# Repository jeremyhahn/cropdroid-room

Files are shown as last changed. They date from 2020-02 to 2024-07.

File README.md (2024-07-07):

# cropdroid-room

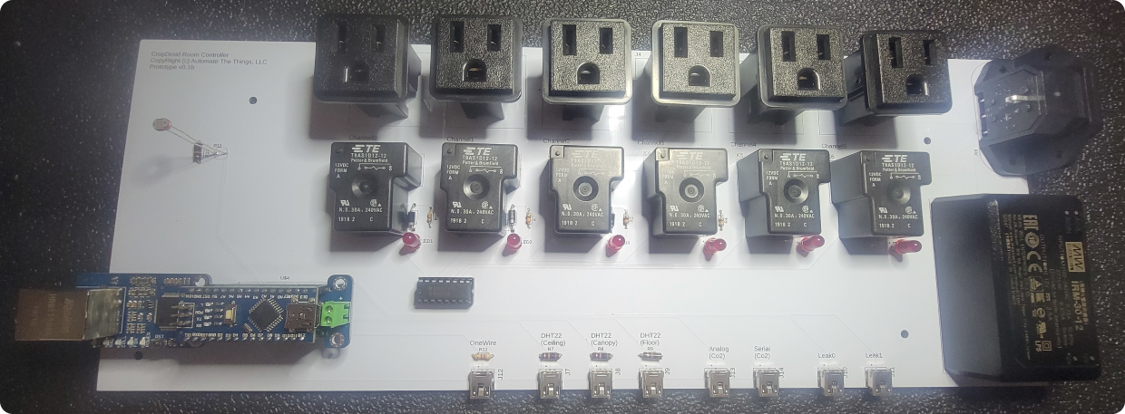
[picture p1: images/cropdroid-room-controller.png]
[](https://github.com/jeremyhahn/cropdroid-room)

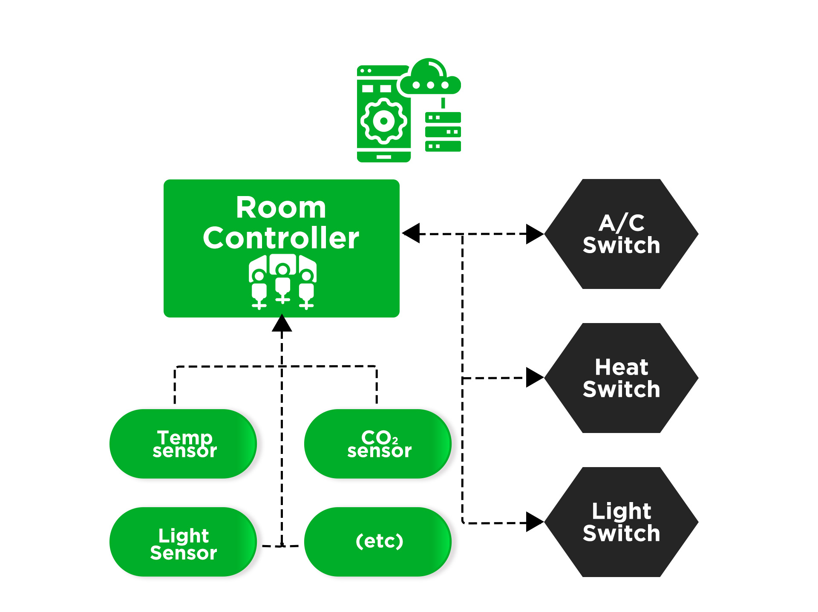
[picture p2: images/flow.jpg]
[](https://github.com/jeremyhahn/cropdroid-room)

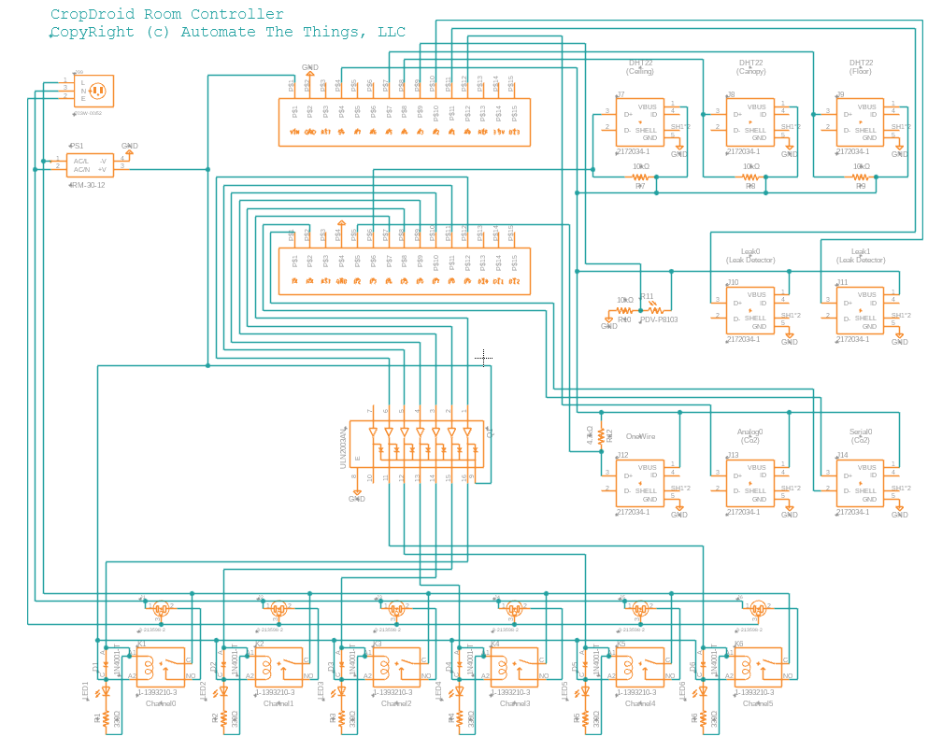
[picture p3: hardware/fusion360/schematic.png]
[](https://github.com/jeremyhahn/cropdroid-room/blob/master/hardware/fusion360/schematic.png)

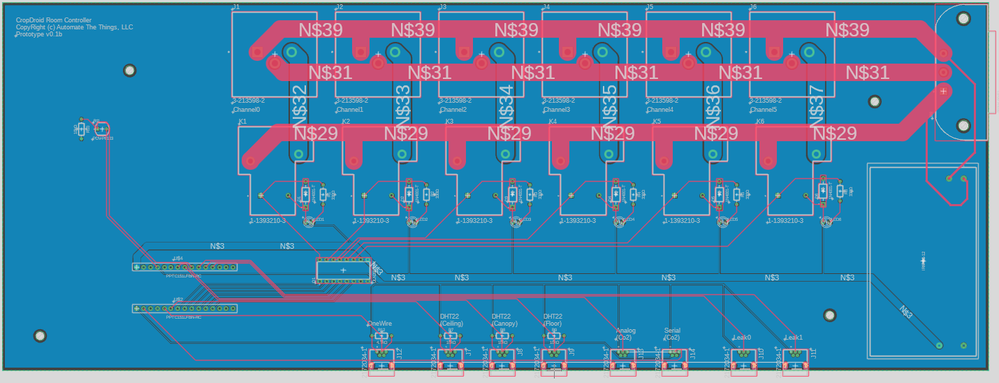
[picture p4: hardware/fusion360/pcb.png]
[](https://github.com/jeremyhahn/cropdroid-room/blob/master/hardware/fusion360/pcb.png)

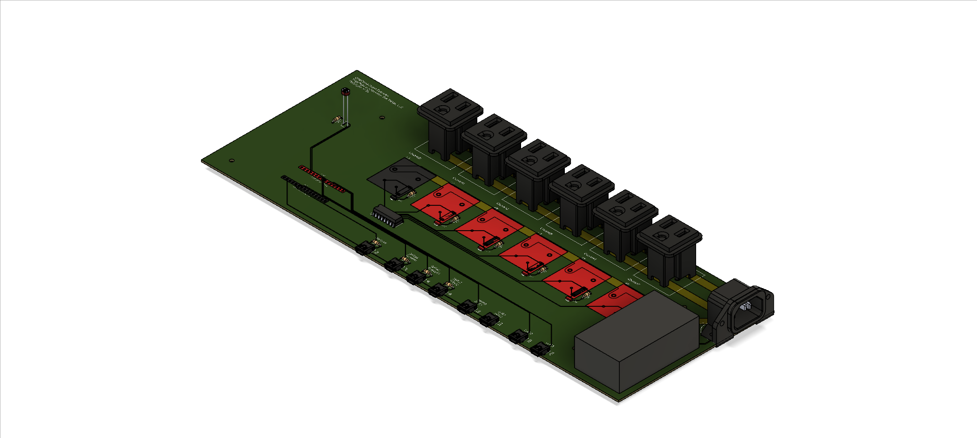
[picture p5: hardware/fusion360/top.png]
[](https://github.com/jeremyhahn/cropdroid-room/blob/master/hardware/fusion360/top.png)

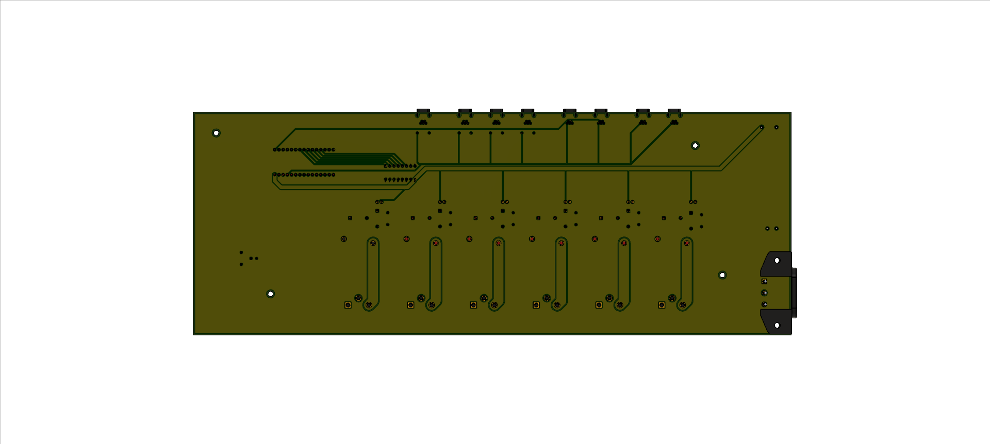
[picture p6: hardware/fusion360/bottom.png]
[](https://github.com/jeremyhahn/cropdroid-room/blob/master/hardware/fusion360/bottom.png)

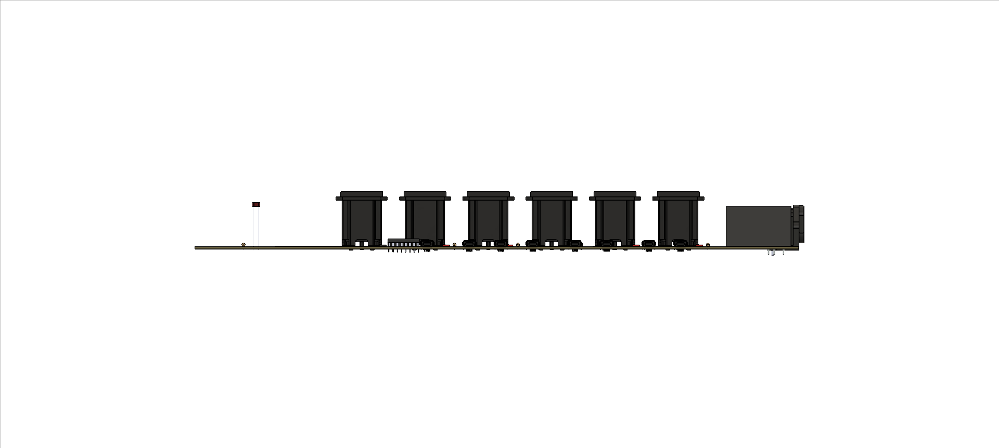
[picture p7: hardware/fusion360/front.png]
[](https://github.com/jeremyhahn/cropdroid-room/blob/master/hardware/fusion360/front.png)

## Support

Please consider supporting this project for ongoing success and sustainability. I'm a passionate open source contributor making a professional living creating free, secure, scalable, robust, enterprise grade, distributed systems and cloud native solutions.

I'm also available for international consulting opportunities. Please let me know how I can assist you or your organization in achieving your desired security posture and technology goals.

https://github.com/sponsors/jeremyhahn

https://www.linkedin.com/in/jeremyhahn

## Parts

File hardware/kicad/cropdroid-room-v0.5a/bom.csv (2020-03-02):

Reference | Quantity | Value | Footprint | Datasheet | Category | DK_Datasheet_Link | DK_Detail_Page | Description | Digi-Key_PN | Family | MPN | Manufacturer | Status | Field4 | Field5 | Field6
D13 | 1 | D_Photo | libraries:PHODET_PDV-P8103 | ~
D3 D5 D7 D9 D1 D11 | 6 | 1N4001 | Diode_THT:D_DO-41_SOD81_P10.16mm_Horizontal | http://www.vishay.com/docs/88503/1n4001.pdf
D4 D6 D8 D10 D2 D12 | 6 | LED | libraries:CAPPRD350W60D800H2000 | ~
J1 | 1 | 703W-00_52 | 703W-00_52:52 | Qualtek |  |  |  |  |  |  |  |  |  | B | Manufacturer Recommendations
J2 J3 J4 J5 J6 J7 | 6 | 3-213598-2 | 3-213598-2:TE_3-213598-2 | https://www.te.com/usa-en/product-3-213598-2.html?te_bu=Cor&te_type=disp&elqCampaignId=32493 |  |  |  |  |  |  |  |  |  | Compliant | 3-213598-2 | Convenience Outlet
J9 J13 J15 J10 J12 J8 J11 J14 | 8 | 2172034-1 | TE_2172034-1 | Compliant |  |  |  |  |  |  |  |  |  | 2172034-1 | https://www.te.com/usa-en/product-2172034-1.html?te_bu=Cor&te_type=disp&elqCampaignId=32493
K2 K3 K4 K5 K1 K6 | 6 | T9AS1D12-15 | T9AS1D12-15:RELAY_T9AS1D12-15 | https://www.te.com/usa-en/product-1-1393210-4.html?te_bu=Cor&te_type=disp&elqCampaignId=32493 |  |  |  |  |  |  |  |  |  | 1-1393210-4
Q1 | 1 | ULN2003AN | digikey-footprints:DIP-16_W7.62mm | http://www.ti.com/general/docs/suppproductinfo.tsp?distId=10 | Discrete Semiconductor Products | http://www.ti.com/general/docs/suppproductinfo.tsp?distId=10 | /product-detail/en/texas-instruments/ULN2003AN/296-1979-5-ND/277624 | IC PWR RELAY 7NPN 1:1 16DIP | 296-1979-5-ND | Transistors - Bipolar (BJT) - Arrays | ULN2003AN | Texas Instruments | Active
R2 R3 R4 R5 R1 R6 | 6 | 1 Ohm | Resistor_THT:R_Axial_DIN0207_L6.3mm_D2.5mm_P10.16mm_Horizontal | ~
R8 | 1 | 10k | Resistor_THT:R_Axial_DIN0207_L6.3mm_D2.5mm_P10.16mm_Horizontal | ~
R9 R10 R11 R7 | 4 | 4.7k | Resistor_THT:R_Axial_DIN0207_L6.3mm_D2.5mm_P10.16mm_Horizontal | ~
U1 | 1 | IRM-30-12 | IRM-30-12:IRM-30-12
U3 U2 | 2 | PPTC151LFBN-RC | PPTC151LFBN-RC:PPTC151LFBN-RC

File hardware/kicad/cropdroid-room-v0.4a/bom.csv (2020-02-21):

Reference | Quantity | Value | Footprint | Datasheet | Category | DK_Datasheet_Link | DK_Detail_Page | Description | Digi-Key_PN | Family | MPN | Manufacturer | Status | Field4 | Field5 | Field6
CON6 CON3 CON5 CON7 CON4 CON2 CON1 | 7 | SJ1-3523N | digikey-footprints:Headphone_Jack_3.5mm_SJ1-3523N | https://www.cui.com/product/resource/digikeypdf/sj1-352xn_series.pdf | Connectors, Interconnects | https://www.cui.com/product/resource/digikeypdf/sj1-352xn_series.pdf | /product-detail/en/cui-inc/SJ1-3523N/CP1-3523N-ND/738689 | CONN JACK STEREO 3.5MM R/A | CP1-3523N-ND | Barrel - Audio Connectors | SJ1-3523N | CUI Inc. | Active
D1 | 1 | 1N5400 | Diode_THT:D_DO-201AD_P15.24mm_Horizontal | http://www.vishay.com/docs/88516/1n5400.pdf
D18 | 1 | D_Photo | libraries:PHODET_PDV-P8103 | ~
D4 D6 D8 D10 D2 D12 D23 D21 D20 D22 D19 D14 D15 D16 | 14 | 1N4001 | Diode_THT:D_DO-41_SOD81_P10.16mm_Horizontal | http://www.vishay.com/docs/88503/1n4001.pdf
D5 D7 D9 D11 D3 D13 | 6 | LED | libraries:CAPPRD350W60D800H2000 | ~
J1 | 1 | 703W-00_52 | 703W-00_52:52 | Qualtek |  |  |  |  |  |  |  |  |  | B | Manufacturer Recommendations
J2 J3 J4 J5 J6 J7 | 6 | 3-213598-2 | 3-213598-2:TE_3-213598-2 | https://www.te.com/usa-en/product-3-213598-2.html?te_bu=Cor&te_type=disp&elqCampaignId=32493 |  |  |  |  |  |  |  |  |  | Compliant | 3-213598-2 | Convenience Outlet
K2 K3 K4 K5 K1 K6 | 6 | T9AS1D12-15 | T9AS1D12-15:RELAY_T9AS1D12-15 | https://www.te.com/usa-en/product-1-1393210-4.html?te_bu=Cor&te_type=disp&elqCampaignId=32493 |  |  |  |  |  |  |  |  |  | 1-1393210-4
Q1 | 1 | ULN2003AN | digikey-footprints:DIP-16_W7.62mm | http://www.ti.com/general/docs/suppproductinfo.tsp?distId=10 | Discrete Semiconductor Products | http://www.ti.com/general/docs/suppproductinfo.tsp?distId=10 | /product-detail/en/texas-instruments/ULN2003AN/296-1979-5-ND/277624 | IC PWR RELAY 7NPN 1:1 16DIP | 296-1979-5-ND | Transistors - Bipolar (BJT) - Arrays | ULN2003AN | Texas Instruments | Active
R2 R3 R4 R5 R1 R6 | 6 | 1 Ohm | Resistor_THT:R_Axial_DIN0207_L6.3mm_D2.5mm_P10.16mm_Horizontal | ~
R8 | 1 | 10k | Resistor_THT:R_Axial_DIN0207_L6.3mm_D2.5mm_P10.16mm_Horizontal | ~
R9 R10 R11 R7 | 4 | 4.7k | Resistor_THT:R_Axial_DIN0207_L6.3mm_D2.5mm_P10.16mm_Horizontal | ~
U1 | 1 | IRM-30-12 | IRM-30-12:IRM-30-12
U3 U2 | 2 | PPTC151LFBN-RC | PPTC151LFBN-RC:PPTC151LFBN-RC

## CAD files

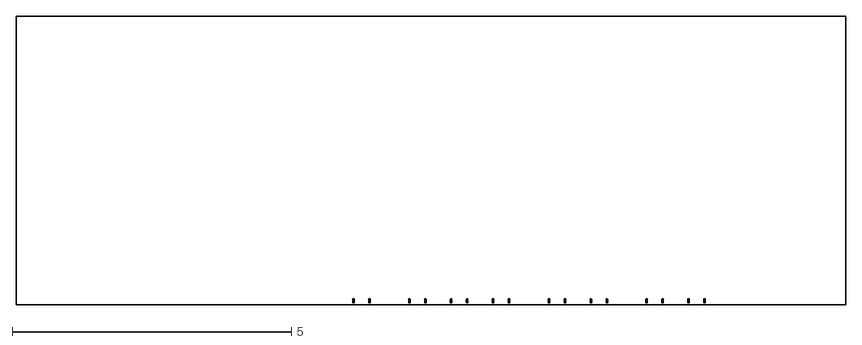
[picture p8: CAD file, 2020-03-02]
hardware/kicad/cropdroid-room-v0.5a/plots/dxf/cropdroid-room-Edge_Cuts.dxf
14.9 x 5.16

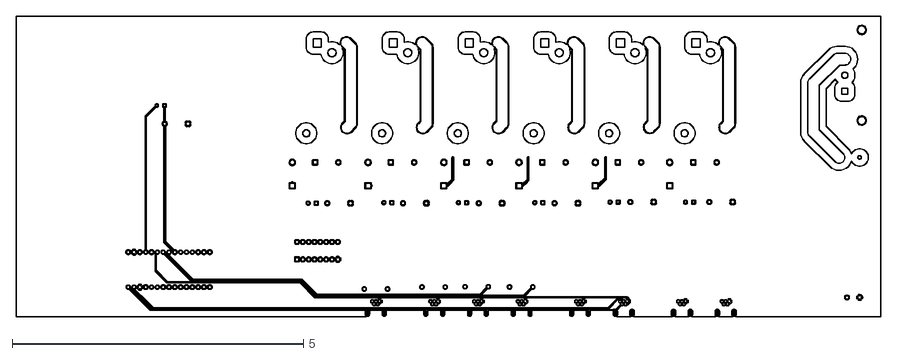
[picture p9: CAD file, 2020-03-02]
hardware/kicad/cropdroid-room-v0.5a/plots/dxf/cropdroid-room-B_Cu.dxf
14.8 x 5.15

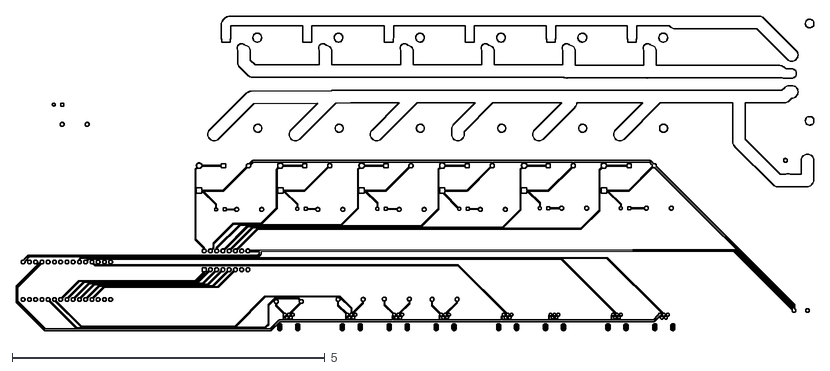
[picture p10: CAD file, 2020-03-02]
hardware/kicad/cropdroid-room-v0.5a/plots/dxf/cropdroid-room-F_Cu.dxf
12.8 x 5.03

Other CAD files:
hardware/kicad/cropdroid-room-v0.5a/plots/dxf/cropdroid-room-B_Mask.dxf
hardware/kicad/cropdroid-room-v0.5a/plots/dxf/cropdroid-room-B_Paste.dxf
hardware/kicad/cropdroid-room-v0.5a/plots/dxf/cropdroid-room-B_SilkS.dxf
hardware/kicad/cropdroid-room-v0.5a/plots/dxf/cropdroid-room-F_Mask.dxf
hardware/kicad/cropdroid-room-v0.5a/plots/dxf/cropdroid-room-F_Paste.dxf

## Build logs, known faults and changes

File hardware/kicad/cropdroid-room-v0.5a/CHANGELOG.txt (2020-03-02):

-v0.5a
- Replace audio jacks with micro usb
- Add serial c02 attached to A6
- Remove extraneous 1N5001 and 1N4001 short circuit protection diodes

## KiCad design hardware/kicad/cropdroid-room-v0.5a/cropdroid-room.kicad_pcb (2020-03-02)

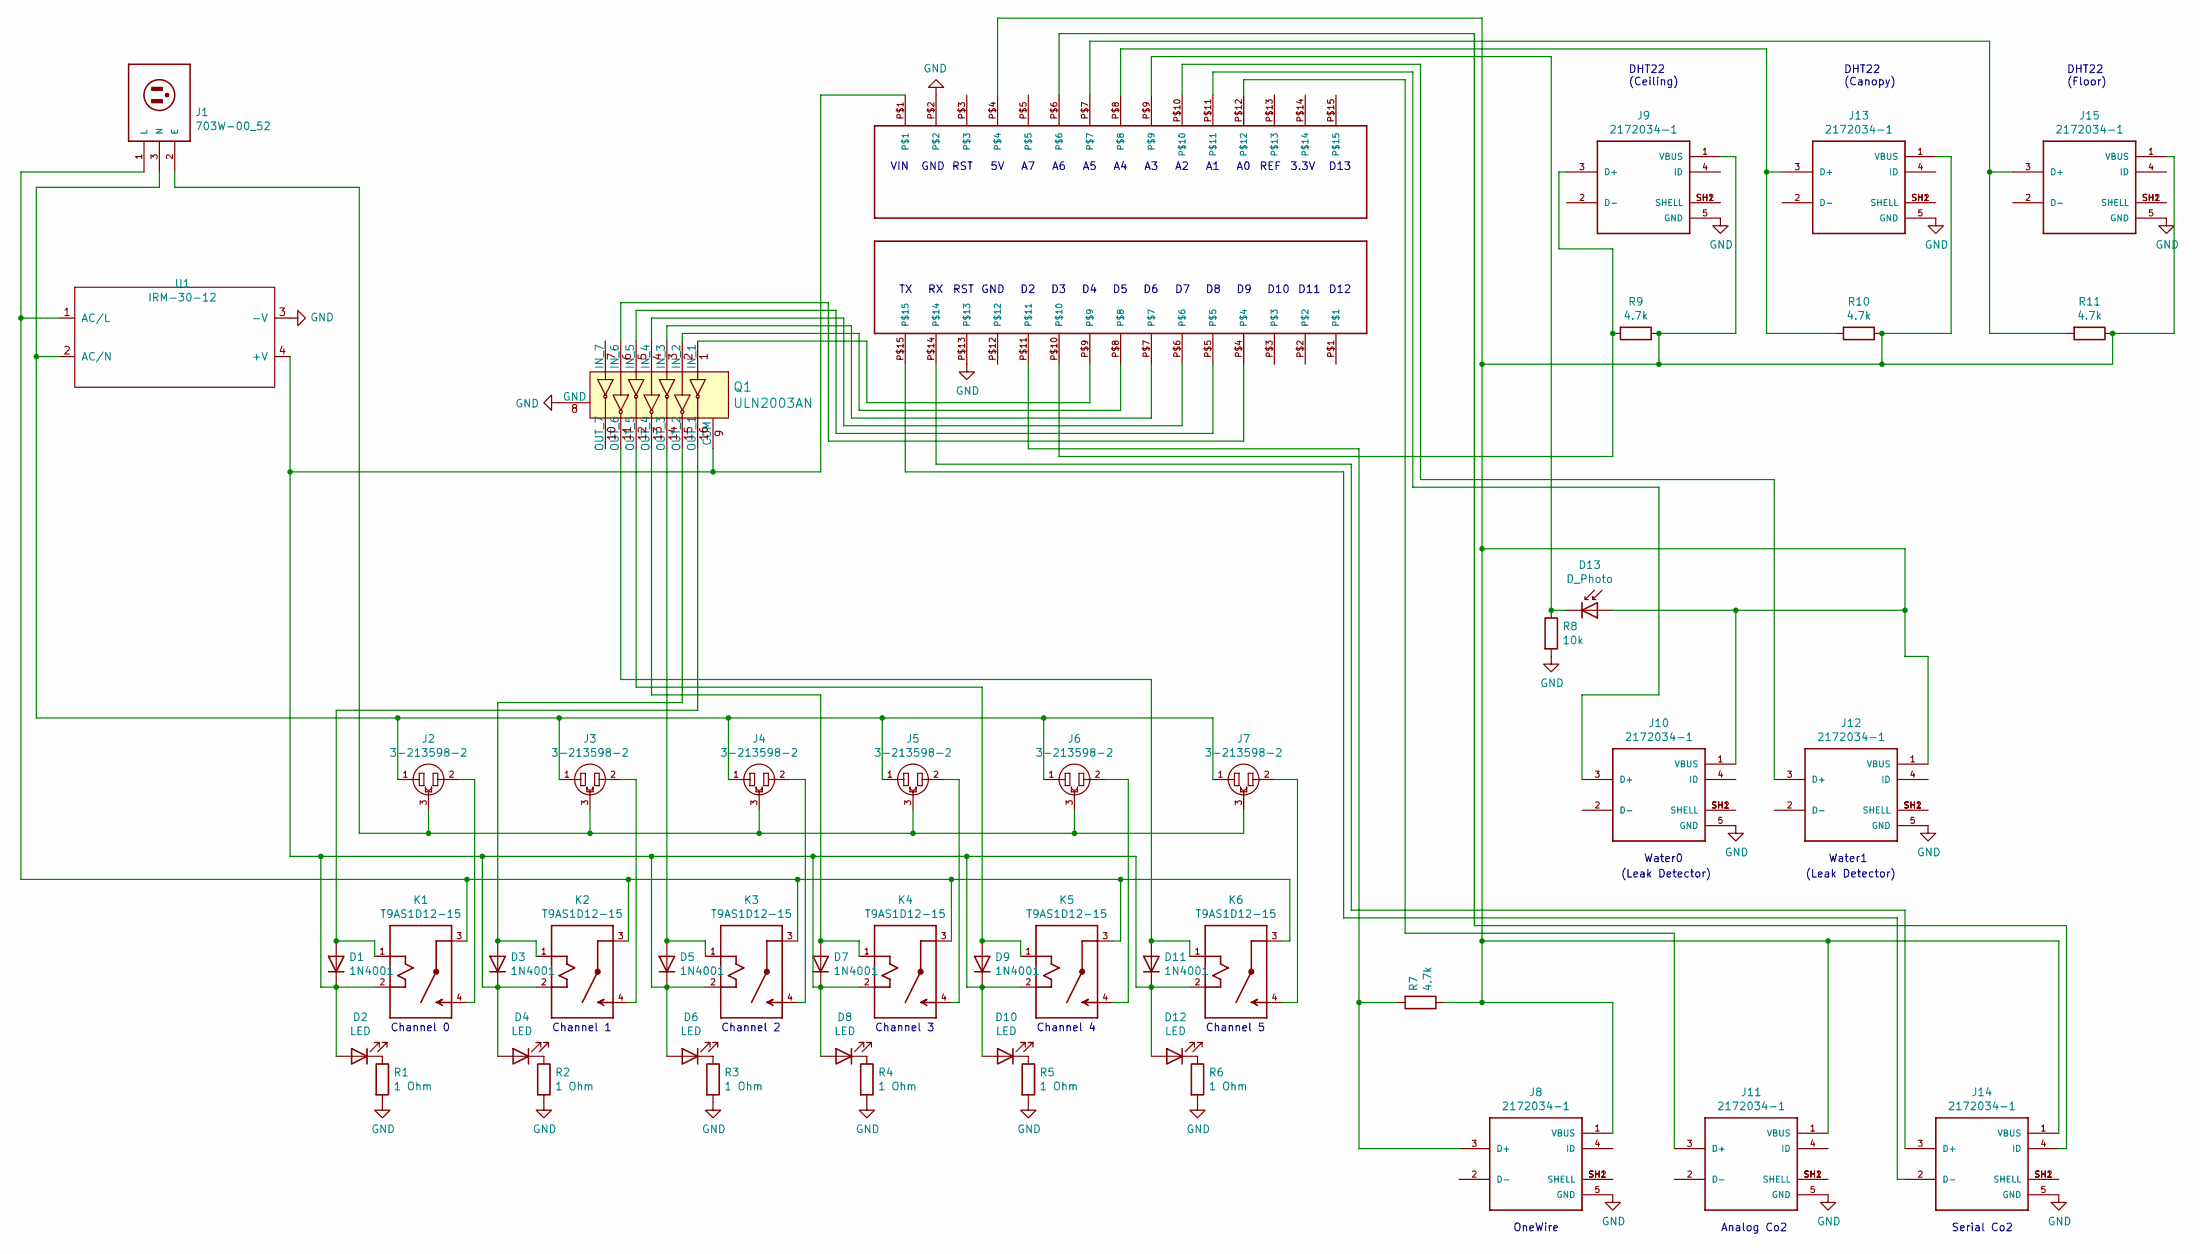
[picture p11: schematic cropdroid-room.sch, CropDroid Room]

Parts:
D1, D3, D5, D7, D9, D11: 1N4001; D_DO-41_SOD81_P10.16mm_Horizontal
D2, D4, D6, D8, D10, D12: LED; CAPPRD350W60D800H2000
D13: D_Photo; PHODET_PDV-P8103
J1: 703W-00_52; 52
J2, J3, J4, J5, J6, J7: 3-213598-2; TE_3-213598-2
J8, J9, J10, J11, J12, J13, J14, J15: 2172034-1; TE_2172034-1
K1, K2, K3, K4, K5, K6: T9AS1D12-15; RELAY_T9AS1D12-15
Q1: ULN2003AN; DIP-16_W7.62mm; MPN ULN2003AN; Digi-Key_PN 296-1979-5-ND
R1, R2, R3, R4, R5, R6: 1 Ohm; R_Axial_DIN0207_L6.3mm_D2.5mm_P10.16mm_Horizontal
R7, R9, R10, R11: 4.7k; R_Axial_DIN0207_L6.3mm_D2.5mm_P10.16mm_Horizontal
R8: 10k; R_Axial_DIN0207_L6.3mm_D2.5mm_P10.16mm_Horizontal
U1: IRM-30-12
U2, U3: PPTC151LFBN-RC

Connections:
GND: J8.5 (GND), J9.5 (GND), J10.5 (GND), J11.5 (GND), J12.5 (GND), J13.5 (GND), J14.5 (GND), J15.5 (GND), Q1.8 (GND), R1.2, R2.2, R3.2, R4.2, R5.2, R6.2, R8.2, U1.3 (-V), U2.P$2, U3.P$13
unnamed: D1.1 (K), D2.2 (A), D3.1 (K), D4.2 (A), D5.1 (K), D6.2 (A), D7.1 (K), D8.2 (A), D9.1 (K), D10.2 (A), D11.1 (K), D12.2 (A), K1.2 (A2), K2.2 (A2), K3.2 (A2), K4.2 (A2), K5.2 (A2), K6.2 (A2), Q1.9 (COM), U1.4 (+V), U2.P$1
unnamed: D1.2 (A), K1.1 (A1), Q1.16 (OUT_1)
unnamed: D2.1 (K), R1.1
unnamed: D3.2 (A), K2.1 (A1), Q1.15 (OUT_2)
unnamed: D4.1 (K), R2.1
unnamed: D5.2 (A), K3.1 (A1), Q1.14 (OUT_3)
unnamed: D6.1 (K), R3.1
unnamed: D7.2 (A), K4.1 (A1), Q1.13 (OUT_4)
unnamed: D8.1 (K), R4.1
unnamed: D9.2 (A), K5.1 (A1), Q1.12 (OUT_5)
unnamed: D10.1 (K), R5.1
unnamed: D11.2 (A), K6.1 (A1), Q1.11 (OUT_6)
unnamed: D12.1 (K), R6.1
unnamed: D13.1 (K), R8.1, U2.P$9
unnamed: D13.2 (A), J8.1 (VBUS), J9.1 (VBUS), J10.1 (VBUS), J11.1 (VBUS), J12.1 (VBUS), J13.1 (VBUS), J14.1 (VBUS), J15.1 (VBUS), R7.1, R9.1, R10.1, R11.1, U2.P$4
unnamed: J1.1 (L), K1.3 (C), K2.3 (C), K3.3 (C), K4.3 (C), K5.3 (C), K6.3 (C), U1.1 (AC/L)
unnamed: J1.2 (E), J2.3, J3.3, J4.3, J5.3, J6.3, J7.3
unnamed: J1.3 (N), J2.1, J3.1, J4.1, J5.1, J6.1, J7.1, U1.2 (AC/N)
unnamed: J2.2, K1.4 (NO)
unnamed: J3.2, K2.4 (NO)
unnamed: J4.2, K3.4 (NO)
unnamed: J5.2, K4.4 (NO)
unnamed: J6.2, K5.4 (NO)
unnamed: J7.2, K6.4 (NO)
unnamed: J8.3 (D+), R7.2, U3.P$11
unnamed: J8.SH1 (SHELL), J8.SH2 (SHELL)
unnamed: J9.3 (D+), R9.2, U3.P$10
unnamed: J9.SH1 (SHELL), J9.SH2 (SHELL)
unnamed: J10.3 (D+), U2.P$11
unnamed: J10.SH1 (SHELL), J10.SH2 (SHELL)
unnamed: J11.3 (D+), U2.P$12
unnamed: J11.SH1 (SHELL), J11.SH2 (SHELL)
unnamed: J12.3 (D+), U2.P$10
unnamed: J12.SH1 (SHELL), J12.SH2 (SHELL)
unnamed: J13.3 (D+), R10.2, U2.P$8
unnamed: J13.SH1 (SHELL), J13.SH2 (SHELL)
unnamed: J14.2 (D-), U3.P$15
unnamed: J14.3 (D+), U3.P$14
unnamed: J14.4 (ID), U2.P$6
unnamed: J14.SH1 (SHELL), J14.SH2 (SHELL)
unnamed: J15.3 (D+), R11.2, U2.P$7
unnamed: J15.SH1 (SHELL), J15.SH2 (SHELL)
unnamed: Q1.1 (IN_1), U3.P$9
unnamed: Q1.2 (IN_2), U3.P$8
unnamed: Q1.3 (IN_3), U3.P$7
unnamed: Q1.4 (IN_4), U3.P$6
unnamed: Q1.5 (IN_5), U3.P$5
unnamed: Q1.6 (IN_6), U3.P$4

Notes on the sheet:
Water0
Water1
(Leak Detector)
Channel 1
Channel 2
Channel 3
Channel 4
Channel 0
DHT22 (Ceiling)
DHT22 (Canopy)
DHT22 (Floor)
Channel 5
D12
D11
D10
D13
3.3V
REF
RST
GND
VIN
Analog Co2
OneWire
Serial Co2

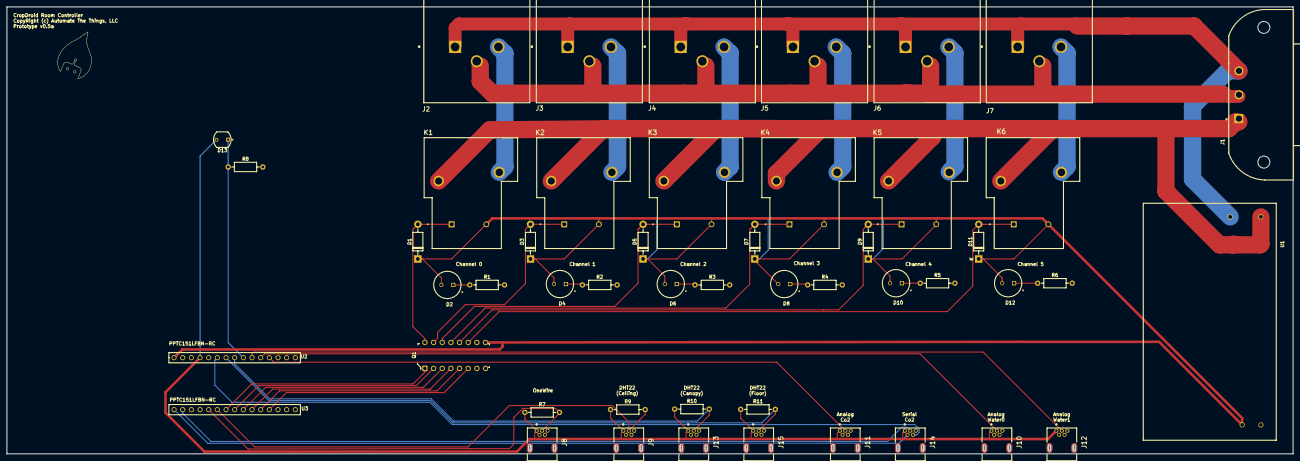
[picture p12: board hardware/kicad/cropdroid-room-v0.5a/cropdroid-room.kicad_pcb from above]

Board: 2 copper layers, 377.2 x 131.1 mm, 49 parts (0 on the bottom side), 49 nets.

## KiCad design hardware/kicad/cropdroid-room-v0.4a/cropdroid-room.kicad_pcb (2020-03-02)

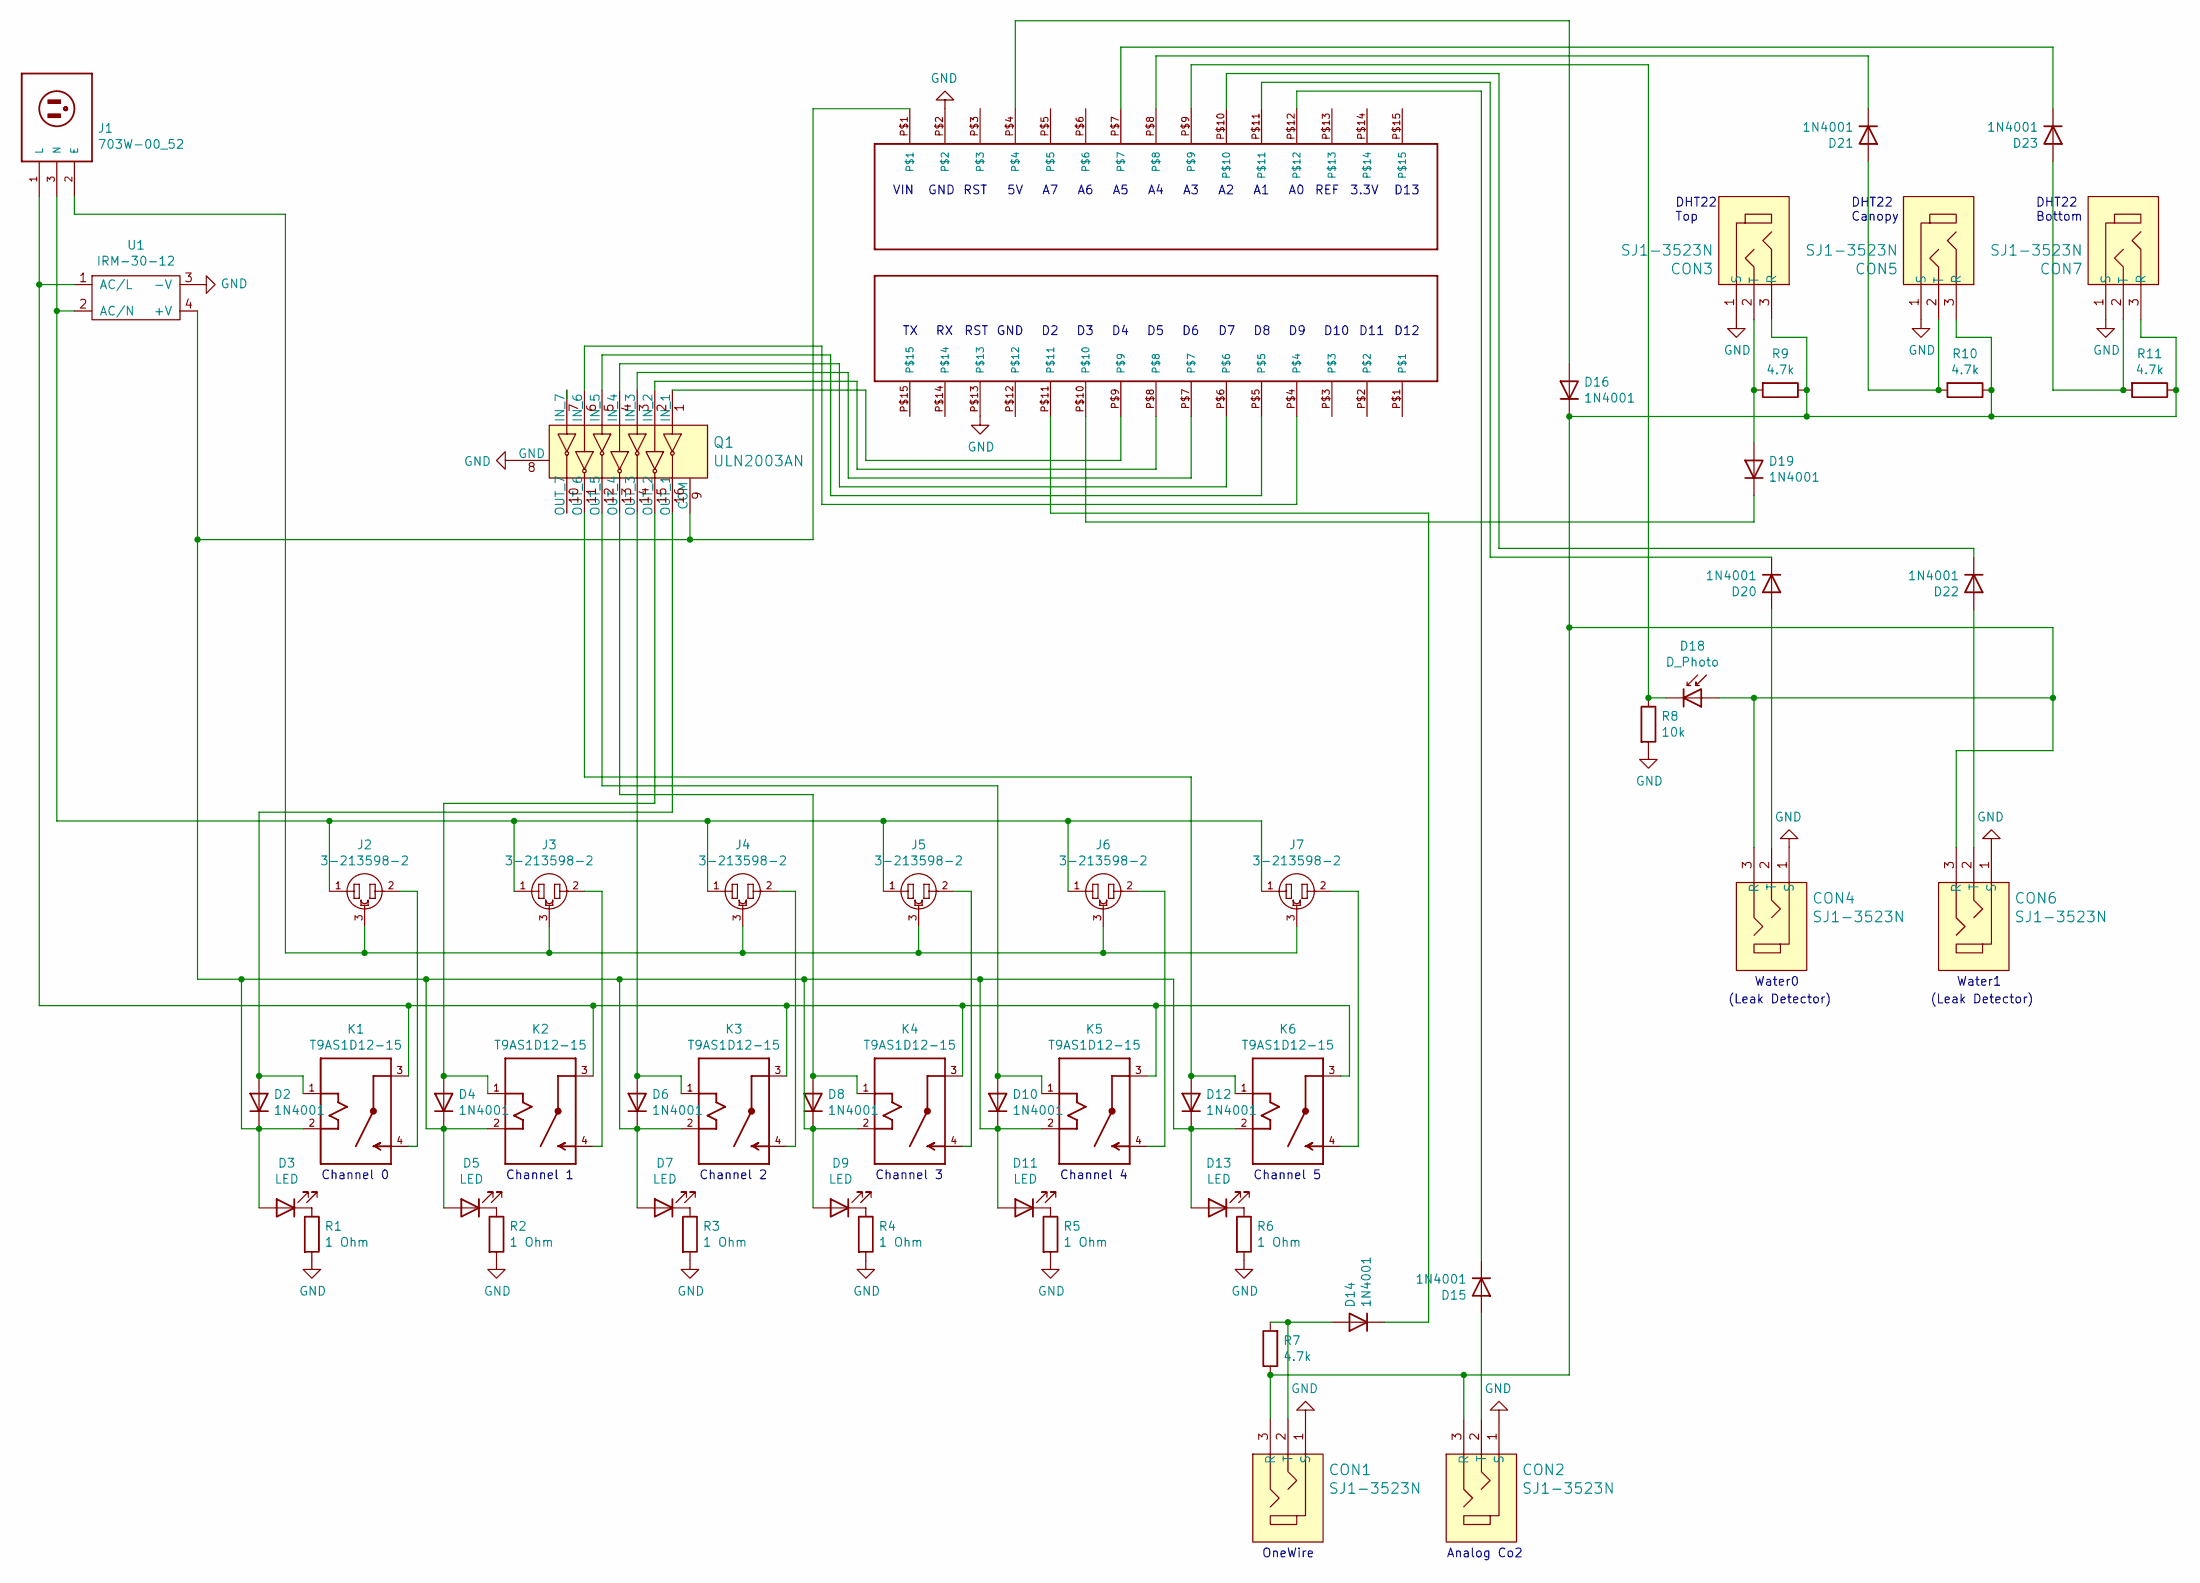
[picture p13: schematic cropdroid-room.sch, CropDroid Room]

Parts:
CON1, CON2, CON3, CON4, CON5, CON6, CON7: SJ1-3523N; Headphone_Jack_3.5mm_SJ1-3523N; MPN SJ1-3523N; Digi-Key_PN CP1-3523N-ND
D2, D4, D6, D8, D10, D12, D14, D15, D16, D19, D20, D21, D22, D23: 1N4001; D_DO-41_SOD81_P10.16mm_Horizontal
D3, D5, D7, D9, D11, D13: LED; CAPPRD350W60D800H2000
D18: D_Photo; PHODET_PDV-P8103
J1: 703W-00_52; 52
J2, J3, J4, J5, J6, J7: 3-213598-2; TE_3-213598-2
K1, K2, K3, K4, K5, K6: T9AS1D12-15; RELAY_T9AS1D12-15
Q1: ULN2003AN; DIP-16_W7.62mm; MPN ULN2003AN; Digi-Key_PN 296-1979-5-ND
R1, R2, R3, R4, R5, R6: 1 Ohm; R_Axial_DIN0207_L6.3mm_D2.5mm_P10.16mm_Horizontal
R7, R9, R10, R11: 4.7k; R_Axial_DIN0207_L6.3mm_D2.5mm_P10.16mm_Horizontal
R8: 10k; R_Axial_DIN0207_L6.3mm_D2.5mm_P10.16mm_Horizontal
U1: IRM-30-12
U2, U3: PPTC151LFBN-RC

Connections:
GND: CON1.1 (S), CON2.1 (S), CON3.1 (S), CON4.1 (S), CON5.1 (S), CON6.1 (S), CON7.1 (S), Q1.8 (GND), R1.2, R2.2, R3.2, R4.2, R5.2, R6.2, R8.2, U1.3 (-V), U2.P$2, U3.P$13
unnamed: CON1.2 (T), D14.2 (A), R7.2
unnamed: CON1.3 (R), CON2.3 (R), CON3.3 (R), CON4.3 (R), CON5.3 (R), CON6.3 (R), CON7.3 (R), D16.1 (K), D18.2 (A), R7.1, R9.1, R10.1, R11.1
unnamed: CON2.2 (T), D15.2 (A)
unnamed: CON3.2 (T), D19.2 (A), R9.2
unnamed: CON4.2 (T), D20.2 (A)
unnamed: CON5.2 (T), D21.2 (A), R10.2
unnamed: CON6.2 (T), D22.2 (A)
unnamed: CON7.2 (T), D23.2 (A), R11.2
unnamed: D2.2 (A), K1.1 (A1), Q1.16 (OUT_1)
unnamed: D3.1 (K), R1.1
unnamed: D4.2 (A), K2.1 (A1), Q1.15 (OUT_2)
unnamed: D5.1 (K), R2.1
unnamed: D6.2 (A), K3.1 (A1), Q1.14 (OUT_3)
unnamed: D7.1 (K), R3.1
unnamed: D8.2 (A), K4.1 (A1), Q1.13 (OUT_4)
unnamed: D9.1 (K), R4.1
unnamed: D2.1 (K), D3.2 (A), D4.1 (K), D5.2 (A), D6.1 (K), D7.2 (A), D8.1 (K), D9.2 (A), D10.1 (K), D11.2 (A), D12.1 (K), D13.2 (A), K1.2 (A2), K2.2 (A2), K3.2 (A2), K4.2 (A2), K5.2 (A2), K6.2 (A2), Q1.9 (COM), U1.4 (+V), U2.P$1
unnamed: D10.2 (A), K5.1 (A1), Q1.12 (OUT_5)
unnamed: D11.1 (K), R5.1
unnamed: D12.2 (A), K6.1 (A1), Q1.11 (OUT_6)
unnamed: D13.1 (K), R6.1
unnamed: D14.1 (K), U3.P$11
unnamed: D15.1 (K), U2.P$12
unnamed: D16.2 (A), U2.P$4
unnamed: D18.1 (K), R8.1, U2.P$9
unnamed: D19.1 (K), U3.P$10
unnamed: D20.1 (K), U2.P$11
unnamed: D21.1 (K), U2.P$8
unnamed: D22.1 (K), U2.P$10
unnamed: D23.1 (K), U2.P$7
unnamed: J1.1 (L), K1.3 (C), K2.3 (C), K3.3 (C), K4.3 (C), K5.3 (C), K6.3 (C), U1.1 (AC/L)
unnamed: J1.2 (E), J2.3, J3.3, J4.3, J5.3, J6.3, J7.3
unnamed: J1.3 (N), J2.1, J3.1, J4.1, J5.1, J6.1, J7.1, U1.2 (AC/N)
unnamed: J2.2, K1.4 (NO)
unnamed: J3.2, K2.4 (NO)
unnamed: J4.2, K3.4 (NO)
unnamed: J5.2, K4.4 (NO)
unnamed: J6.2, K5.4 (NO)
unnamed: J7.2, K6.4 (NO)
unnamed: Q1.1 (IN_1), U3.P$9
unnamed: Q1.2 (IN_2), U3.P$8
unnamed: Q1.3 (IN_3), U3.P$7
unnamed: Q1.4 (IN_4), U3.P$6
unnamed: Q1.5 (IN_5), U3.P$5
unnamed: Q1.6 (IN_6), U3.P$4

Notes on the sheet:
Water0
Water1
(Leak Detector)
Channel 1
Channel 2
Channel 3
Channel 4
Channel 0
DHT22 Top
DHT22 Canopy
DHT22 Bottom
Channel 5
D12
D11
D10
D13
3.3V
REF
RST
GND
VIN
OneWire
Analog Co2

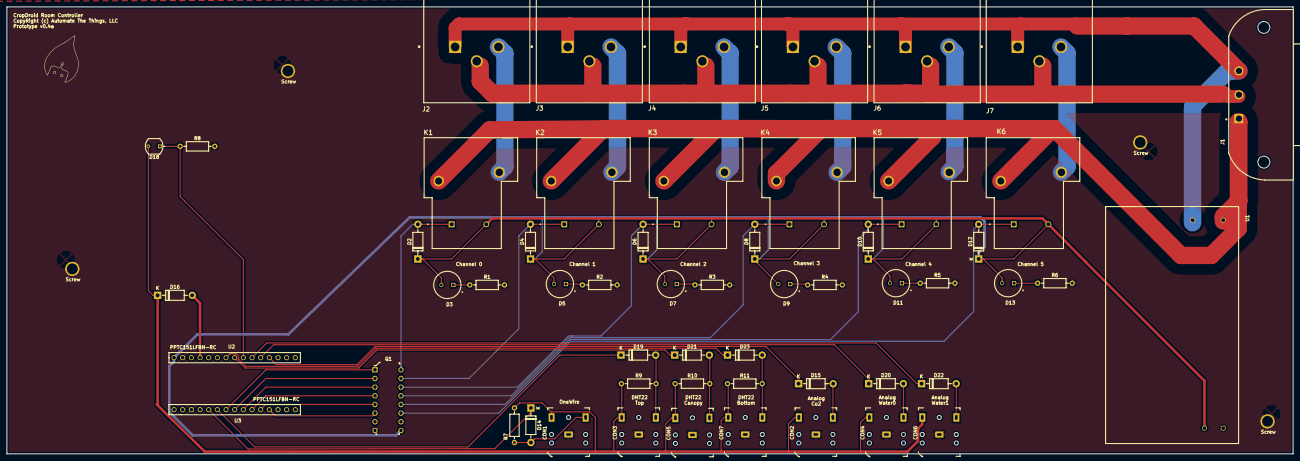
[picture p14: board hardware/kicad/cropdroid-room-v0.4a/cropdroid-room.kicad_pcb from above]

Board: 2 copper layers, 377.2 x 131.1 mm, 60 parts (0 on the bottom side), 46 nets.

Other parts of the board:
Screw: Drill; Drill_Hole
Screw#2, Screw#3, Screw#4: Drill; Drill_Hole

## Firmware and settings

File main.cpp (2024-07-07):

// SPDX-License-Identifier: AGPL-3.0-or-later
// SPDX-License-Identifier: commercial

#include <stdio.h>
#include <Arduino.h>
#include <Ethernet.h>
#include "DHT.h"
#include "OneWire.h"
#include "DallasTemperature.h"
#include "EEPROM.h"

#define DEBUG 0
#define EEPROM_DEBUG 1
#define BUFSIZE 100
#define CHANNEL_SIZE 6

#define ONE_WIRE_BUS 2
#define DHT_ROOM_PIN1 3
#define ANALOG_CO2_PIN A0
#define WATER0_PIN A1
#define WATER1_PIN A2
#define PHOTO_PIN A3
#define DHT_ROOM_PIN2 A4
#define DHT_ROOM_PIN3 A5

extern int  __bss_end;
extern int  *__brkval;

const int NULL_CHANNEL = 255;
const int channels[CHANNEL_SIZE] = {
	4, 5, 6, 7, 8, 9
};
unsigned long channel_table[CHANNEL_SIZE][3] = {
	// channel, start, interval
   {NULL_CHANNEL, 0, 0},
   {NULL_CHANNEL, 0, 0},
   {NULL_CHANNEL, 0, 0},
   {NULL_CHANNEL, 0, 0},
   {NULL_CHANNEL, 0, 0},
   {NULL_CHANNEL, 0, 0} // 6
};

const char json_bracket_open[] = "{";
const char json_bracket_close[] = "}";
const char json_array_bracket_close[] = "]";
const char json_comma[] = ",";

const char string_initializing[] PROGMEM = "Initializing room...";
const char string_dhcp_failed[] PROGMEM = "DHCP Failed";
const char string_http_200[] PROGMEM = "HTTP/1.1 200 OK";
const char string_http_404[] PROGMEM = "HTTP/1.1 404 Not Found";
const char string_http_500[] PROGMEM = "HTTP/1.1 500 Internal Server Error";
const char string_http_content_type_json[] PROGMEM = "Content-Type: application/json";
const char string_http_xpowered_by[] PROGMEM = "X-Powered-By: CropDroid";
const char string_rest_address[] PROGMEM = "REST service listening on: ";
const char string_switch_on[] PROGMEM = "Switching on";
const char string_switch_off[] PROGMEM = "Switching off";
const char string_json_key_mem[] PROGMEM = "\"mem\":";
const char string_json_key_tempF0[] PROGMEM = ",\"tempF0\":";
const char string_json_key_tempC0[] PROGMEM = ",\"tempC0\":";
const char string_json_key_humidity0[] PROGMEM = ",\"humidity0\":";
const char string_json_key_heatIndex0[] PROGMEM = ",\"heatIndex0\":";
const char string_json_key_tempF1[] PROGMEM = ",\"tempF1\":";
const char string_json_key_tempC1[] PROGMEM = ",\"tempC1\":";
const char string_json_key_humidity1[] PROGMEM = ",\"humidity1\":";
const char string_json_key_heatIndex1[] PROGMEM = ",\"heatIndex1\":";
const char string_json_key_tempF2[] PROGMEM = ",\"tempF2\":";
const char string_json_key_tempC2[] PROGMEM = ",\"tempC2\":";
const char string_json_key_humidity2[] PROGMEM = ",\"humidity2\":";
const char string_json_key_heatIndex2[] PROGMEM = ",\"heatIndex2\":";
const char string_json_key_vpd[] PROGMEM = ",\"vpd\":";
const char string_json_key_water0[] PROGMEM = ",\"water0\":";
const char string_json_key_water1[] PROGMEM = ",\"water1\":";
const char string_json_key_co2[] PROGMEM = ",\"co2\":";
const char string_json_key_leak0[] PROGMEM = ",\"leak0\":";
const char string_json_key_leak1[] PROGMEM = ",\"leak1\":";
const char string_json_key_photo[] PROGMEM = ",\"photo\":";
const char string_json_key_metrics[] PROGMEM = "\"metrics\":{";
const char string_json_key_channels[] PROGMEM = ",\"channels\":[";
const char string_json_key_channel[] PROGMEM = "\"channel\":";
const char string_json_key_pin[] PROGMEM = ",\"pin\":";
const char string_json_key_position[] PROGMEM =  ",\"position\":";
const char string_json_key_value[] PROGMEM =  ",\"value\":";
const char string_json_key_address[] PROGMEM =  "\"address\":";
const char string_json_bracket_open[] PROGMEM = "{";
const char string_json_bracket_close[] PROGMEM = "}";
const char string_json_error_invalid_channel[] PROGMEM = "\"error\":\"Invalid channel\"";
const char string_json_reboot_true PROGMEM = "\"reboot\":true";
const char string_json_reset_true PROGMEM = "\"reset\":true";
const char string_hardware_version[] PROGMEM = "\"hardware\":\"room-v0.1b\",";
const char string_firmware_version[] PROGMEM = "\"firmware\":\"1.0.0b\"";
const char string_json_key_uptime[] PROGMEM = ",\"uptime\":";
const char * const string_table[] PROGMEM = {
  string_initializing,
  string_dhcp_failed,
  string_http_200,
  string_http_404,
  string_http_500,
  string_http_content_type_json,
  string_http_xpowered_by,
  string_rest_address,
  string_switch_on,
  string_switch_off,
  string_json_key_mem,
  string_json_key_tempF0,
  string_json_key_tempC0,
  string_json_key_humidity0,
  string_json_key_heatIndex0,
  string_json_key_tempF1,
  string_json_key_tempC1,
  string_json_key_humidity1,
  string_json_key_heatIndex1,
  string_json_key_tempF2,
  string_json_key_tempC2,
  string_json_key_humidity2,
  string_json_key_heatIndex2,
  string_json_key_vpd,
  string_json_key_water0,
  string_json_key_water1,
  string_json_key_co2,
  string_json_key_leak0,
  string_json_key_leak1,
  string_json_key_photo,
  string_json_key_metrics,
  string_json_key_channels,
  string_json_key_channel,
  string_json_key_pin,
  string_json_key_position,
  string_json_key_value,
  string_json_key_address,
  string_json_bracket_open,
  string_json_bracket_close,
  string_json_error_invalid_channel,
  string_json_reboot_true,
  string_json_reset_true,
  string_hardware_version,
  string_firmware_version,
  string_json_key_uptime
};
int idx_initializing = 0,
    idx_dhcp_failed = 1,
	idx_http_200 = 2,
	idx_http_404 = 3,
	idx_http_500 = 4,
	idx_http_content_type_json = 5,
	idx_http_xpowered_by = 6,
	idx_rest_address = 7,
	idx_switch_on = 8,
	idx_switch_off = 9,
	idx_json_key_mem = 10,
	idx_json_key_tempF0 = 11,
	idx_json_key_tempC0 = 12,
	idx_json_key_humidity0 = 13,
	idx_json_key_heatIndex0 = 14,
	idx_json_key_tempF1 = 15,
	idx_json_key_tempC1 = 16,
	idx_json_key_humidity1 = 17,
	idx_json_key_heatIndex1 = 18,
	idx_json_key_tempF2 = 19,
	idx_json_key_tempC2 = 20,
	idx_json_key_humidity2 = 21,
	idx_json_key_heatIndex2 = 22,
	idx_json_key_vpd = 23,
	idx_json_key_water0 = 24,
	idx_json_key_water1 = 25,
	idx_json_key_co2 = 26,
	idx_json_key_leak0 = 27,
	idx_json_key_leak1 = 28,
	idx_json_key_photo = 29,
	idx_json_key_metrics = 30,
	idx_json_key_channels = 31,
	idx_json_key_channel = 32,
	idx_json_key_pin = 33,
	idx_json_key_position = 34,
	idx_json_key_value = 35,
	idx_json_key_address = 36,
	idx_json_key_bracket_open = 37,
	idx_json_key_bracket_close = 38,
	idx_json_error_invalid_channel = 39,
	idx_json_reboot_true = 40,
	idx_json_reset_true = 41,
	idx_hardware_version = 42,
	idx_firmware_version = 43,
	idx_json_key_uptime = 44;
char string_buffer[50];
char float_buffer[10];

OneWire oneWire(ONE_WIRE_BUS);
DallasTemperature sensors(&oneWire);
DHT roomDHT0(DHT_ROOM_PIN1, DHT22);
DHT roomDHT1(DHT_ROOM_PIN2, DHT22);
DHT roomDHT2(DHT_ROOM_PIN3, DHT22);

float roomTempF0, roomTempC0, roomHumidity0, roomHeatIndex0,
	  roomTempF1, roomTempC1, roomHumidity1, roomHeatIndex1,
	  roomTempF2, roomTempC2, roomHumidity2, roomHeatIndex2,
      water0Temp, water1Temp, CO2PPM, VPD = 0.0;

int waterLevel0, waterLevel1, photo = 0;

void readRoomTempHumidity();
void calculateVPD(float temp, float rh);
void readPodTemps();
void readPhoto();
void co2ppm();
void readWaterLevels();
void handleWebRequest();
void send404();
void switchOn(int pin);
void switchOff(int pin);
void resetDefaults();
int availableMemory();
void(* resetFunc) (void) = 0;

byte defaultMac[] = { 0x04, 0x02, 0x00, 0x00, 0x00, 0x01 };

byte mac[] = {
	EEPROM.read(0),
	EEPROM.read(1),
	EEPROM.read(2),
	EEPROM.read(3),
	EEPROM.read(4),
	EEPROM.read(5)
};
IPAddress ip(
  EEPROM.read(6),
  EEPROM.read(7),
  EEPROM.read(8),
  EEPROM.read(9));

EthernetServer httpServer(80);
EthernetClient httpClient;

int main(void) {
  init();
  setup();;

  for (;;)
    loop();

  return 0;
}

void setup(void) {

  //EEPROM.write(0, 255);

  #if DEBUG || EEPROM_DEBUG
    Serial.begin(115200);

    strcpy_P(string_buffer, (char*)pgm_read_word(&(string_table[idx_initializing])));
    Serial.println(string_buffer);
  #endif

  analogReference(DEFAULT);

  for(int i=0; i<CHANNEL_SIZE; i++) {
	pinMode(channels[i], OUTPUT);
	digitalWrite(channels[i], LOW);
  }

  byte macByte1 = EEPROM.read(0);

  #if DEBUG || EEPROM_DEBUG
    Serial.print("EEPROM(0):");
    Serial.println(macByte1);
  #endif

  if(macByte1 == 255) {
	resetDefaults();
    if(Ethernet.begin(defaultMac) == 0) {
	  #if DEBUG
	    strcpy_P(string_buffer, (char*)pgm_read_word(&(string_table[idx_dhcp_failed])));
		Serial.println(string_buffer);
	  #endif
	  return;
	}
  }
  else {
    Ethernet.begin(mac, ip);
  }

  #if DEBUG || EEPROM_DEBUG
    Serial.print("MAC:");
    for(int i=0; i<6; i++) {
      Serial.print(mac[i], HEX);
    }
    Serial.println();

    strcpy_P(string_buffer, (char*)pgm_read_word(&(string_table[idx_rest_address])));
    Serial.print(string_buffer);
    Serial.println(Ethernet.localIP());
  #endif

  httpServer.begin();
  roomDHT0.begin();
  roomDHT1.begin();
  roomDHT2.begin();
}

void loop() {

  digitalWrite(LED_BUILTIN, HIGH);

  sensors.requestTemperatures();
  readPodTemps();
  readRoomTempHumidity();
  readPhoto();
  calculateVPD(roomTempC0, roomHumidity0);
  co2ppm();
  readWaterLevels();

  handleWebRequest();

  digitalWrite(LED_BUILTIN, LOW);

  delay(2000); // DHT22 requires min 2 seconds between polls
}

void calculateVPD(float temp, float rh) {
  //float es = 0.6108 * exp(17.27 * temp / (temp + 237.3));
  //float ea = rh / 100 * es;
  //VPD = ea - es;

  float es = 0.6107 * exp(7.5 * temp / (temp + 237.3));
  float ea = rh / 100 * es;
  VPD = ea - es;

  //float svp = 610.78 * exp(temp / (temp + 238.3) * 17.2694);
  //VPD = svp * (1 - rh / 100);

#if DEBUG
  Serial.print("VPD:");
  Serial.println(VPD);
#endif
}

void readPodTemps() {
  water0Temp = sensors.getTempFByIndex(0);
  water1Temp = sensors.getTempFByIndex(1);

#if DEBUG
  Serial.print("water0:");
  Serial.println(water0Temp);
  Serial.print("water1:");
  Serial.println(water1Temp);
#endif
}

void readPhoto() {
  photo = analogRead(PHOTO_PIN);
#if DEBUG
  Serial.print("Photo:");
  Serial.println(photo);
#endif
}

float zeroIfNan(float number) {
  if(isnan(number)) {
	number = 0.0;
  }
  return number;
}

void readRoomTempHumidity() {

  roomTempC0 = zeroIfNan(roomDHT0.readTemperature(false));
  roomTempF0 = zeroIfNan(roomDHT0.convertCtoF(roomTempC0));
  roomHumidity0 = zeroIfNan(roomDHT0.readHumidity());
  roomHeatIndex0 = zeroIfNan(roomDHT0.computeHeatIndex(roomTempF0, roomHumidity0));

  roomTempC1 = zeroIfNan(roomDHT1.readTemperature(false));
  roomTempF1 = zeroIfNan(roomDHT1.convertCtoF(roomTempC1));
  roomHumidity1 = zeroIfNan(roomDHT1.readHumidity());
  roomHeatIndex1 = zeroIfNan(roomDHT1.computeHeatIndex(roomTempF1, roomHumidity1));

  roomTempC2 = zeroIfNan(roomDHT2.readTemperature(false));
  roomTempF2 = zeroIfNan(roomDHT2.convertCtoF(roomTempC2));
  roomHumidity2 = zeroIfNan(roomDHT2.readHumidity());
  roomHeatIndex2 = zeroIfNan(roomDHT2.computeHeatIndex(roomTempF2, roomHumidity2));

#if DEBUG
  Serial.print("TempF:");
  Serial.println(roomTempF0);
  Serial.print("TempC:");
  Serial.println(roomTempC0);
  Serial.print("Humidity:");
  Serial.println(roomHumidity0);
  Serial.print("HeatIndex:");
  Serial.println(roomHeatIndex0);
#endif
}

void co2ppm() {

  int sensorValue = analogRead(ANALOG_CO2_PIN);
  float voltage = sensorValue * (5000 / 1024.0);

  if(voltage == 0) {
	#if DEBUG
      Serial.println("CO2 Fault");
	#endif
  }
  else if(voltage < 400) {
	#if DEBUG
      Serial.println("Preheating CO2 sensor");
	#endif
  }
  else {
    int voltage_diference = voltage - 400;
    float concentration = voltage_diference *50.0 / 16.0;
	#if DEBUG
	  Serial.print("co2 voltage:");
	  Serial.print(voltage);
	  Serial.println("mv");
	  Serial.print(concentration);
	  Serial.println("ppm");
	#endif
    CO2PPM = concentration;
  }
}

void readWaterLevels() {

  waterLevel0 = analogRead(WATER0_PIN) * 100 / 1024;
  waterLevel1 = analogRead(WATER1_PIN) * 100 / 1024;

#if DEBUG

  itoa(waterLevel0, float_buffer, 10);
  strcpy(string_buffer, "leak0:");
  strcat(string_buffer, float_buffer);
  strcat(string_buffer, "%");
  Serial.println(string_buffer);

  itoa(waterLevel1, float_buffer, 10);
  strcpy(string_buffer, "leak1:");
  strcat(string_buffer, float_buffer);
  strcat(string_buffer, "%");
  Serial.println(string_buffer);

#endif
}

void switchOn(int pin) {
#if DEBUG
  char sPin[3];
  itoa(pin, sPin, 10);
  strcpy_P(string_buffer, (char*)pgm_read_word(&(string_table[idx_switch_on])));
  strcat(string_buffer, " pin ");
  strcat(string_buffer, sPin);
  Serial.println(string_buffer);
#endif
  digitalWrite(pin, HIGH);
}

void switchOff(int pin) {
#if DEBUG
  char sPin[3];
  itoa(pin, sPin, 10);
  strcpy_P(string_buffer, (char*)pgm_read_word(&(string_table[idx_switch_off])));
  strcat(string_buffer, " pin ");
  strcat(string_buffer, sPin);
  Serial.println(string_buffer);
#endif
  digitalWrite(pin, LOW);
}

void handleWebRequest() {

	unsigned long currentMillis = millis();

	for(int i=0; i<CHANNEL_SIZE; i++) {
		if(channel_table[i][0] != NULL_CHANNEL) {
			if(currentMillis - channel_table[i][1] > channel_table[i][2]) {

				digitalWrite(channel_table[i][0], LOW);

				#if DEBUG
				  Serial.print("Channel ");
				  Serial.print(i);
				  Serial.print(" (pin ");
				  Serial.print(channel_table[i][0]);
				  Serial.print(") off after ");
				  Serial.print(channel_table[i][2] / 1000);
				  Serial.println(" seconds");
				#endif

				channel_table[i][0] = NULL_CHANNEL;
				channel_table[i][1] = 0;
				channel_table[i][2] = 0;
			}
		}
	}

	httpClient = httpServer.available();

	char clientline[BUFSIZE] = {0};
	int index = 0;

	bool reboot = false;
	char json[375];
	char sPin[3];
	char state[3];

	if (httpClient) {

		// reset input buffer
		index = 0;

		while (httpClient.connected()) {

			if (httpClient.available()) {

				char c = httpClient.read();
				if (c != '\n' && c != '\r' && index < BUFSIZE) {
					clientline[index++] = c;
					continue;
				}

				httpClient.flush();

				String urlString = String(clientline);
				String op = urlString.substring(0, urlString.indexOf(' '));
				urlString = urlString.substring(urlString.indexOf('/'), urlString.indexOf(' ', urlString.indexOf('/')));
				urlString.toCharArray(clientline, BUFSIZE);

				char *resource = strtok(clientline, "/");
				char *param1 = strtok(NULL, "/");
				char *param2 = strtok(NULL, "/");

				#if DEBUG
				  Serial.print("Resource: ");
				  Serial.println(resource);

				  Serial.print("Param1: ");
				  Serial.println(param1);

				  Serial.print("Param2: ");
				  Serial.println(param2);
				#endif

				// /state
				if (strncmp(resource, "state", 5) == 0) {

					strcpy(json, json_bracket_open);

					  strcpy_P(string_buffer, (char*)pgm_read_word(&(string_table[idx_json_key_metrics])));
					  strcat(json, string_buffer);

					    strcpy_P(string_buffer, (char*)pgm_read_word(&(string_table[idx_json_key_mem])));
					    strcat(json, string_buffer);
					    itoa(availableMemory(), float_buffer, 10);
					    strcat(json, float_buffer);

					    strcpy_P(string_buffer, (char*)pgm_read_word(&(string_table[idx_json_key_tempF0])));
					    strcat(json, string_buffer);
					    dtostrf(roomTempF0, 4, 2, float_buffer);
					    strcat(json, float_buffer);

					    strcpy_P(string_buffer, (char*)pgm_read_word(&(string_table[idx_json_key_tempC0])));
					    strcat(json, string_buffer);
					    dtostrf(roomTempC0, 4, 2, float_buffer);
					    strcat(json, float_buffer);

					    strcpy_P(string_buffer, (char*)pgm_read_word(&(string_table[idx_json_key_humidity0])));
					    strcat(json, string_buffer);
					    dtostrf(roomHumidity0, 4, 2, float_buffer);
					    strcat(json, float_buffer);

					    strcpy_P(string_buffer, (char*)pgm_read_word(&(string_table[idx_json_key_heatIndex0])));
					    strcat(json, string_buffer);
					    dtostrf(roomHeatIndex0, 4, 2, float_buffer);
					    strcat(json, float_buffer);

					    strcpy_P(string_buffer, (char*)pgm_read_word(&(string_table[idx_json_key_tempF1])));
					    strcat(json, string_buffer);
					    dtostrf(roomTempF1, 4, 2, float_buffer);
					    strcat(json, float_buffer);

					    strcpy_P(string_buffer, (char*)pgm_read_word(&(string_table[idx_json_key_tempC1])));
					    strcat(json, string_buffer);
					    dtostrf(roomTempC1, 4, 2, float_buffer);
					    strcat(json, float_buffer);

					    strcpy_P(string_buffer, (char*)pgm_read_word(&(string_table[idx_json_key_humidity1])));
					    strcat(json, string_buffer);
					    dtostrf(roomHumidity1, 4, 2, float_buffer);
					    strcat(json, float_buffer);

					    strcpy_P(string_buffer, (char*)pgm_read_word(&(string_table[idx_json_key_heatIndex1])));
					    strcat(json, string_buffer);
					    dtostrf(roomHeatIndex1, 4, 2, float_buffer);
					    strcat(json, float_buffer);

					    strcpy_P(string_buffer, (char*)pgm_read_word(&(string_table[idx_json_key_tempF2])));
					    strcat(json, string_buffer);
					    dtostrf(roomTempF2, 4, 2, float_buffer);
					    strcat(json, float_buffer);

					    strcpy_P(string_buffer, (char*)pgm_read_word(&(string_table[idx_json_key_tempC2])));
					    strcat(json, string_buffer);
					    dtostrf(roomTempC2, 4, 2, float_buffer);
					    strcat(json, float_buffer);

					    strcpy_P(string_buffer, (char*)pgm_read_word(&(string_table[idx_json_key_humidity2])));
					    strcat(json, string_buffer);
					    dtostrf(roomHumidity2, 4, 2, float_buffer);
					    strcat(json, float_buffer);

					    strcpy_P(string_buffer, (char*)pgm_read_word(&(string_table[idx_json_key_heatIndex2])));
					    strcat(json, string_buffer);
					    dtostrf(roomHeatIndex2, 4, 2, float_buffer);
					    strcat(json, float_buffer);

					    strcpy_P(string_buffer, (char*)pgm_read_word(&(string_table[idx_json_key_vpd])));
					    strcat(json, string_buffer);
					    dtostrf(VPD, 4, 2, float_buffer);
					    strcat(json, float_buffer);

					    strcpy_P(string_buffer, (char*)pgm_read_word(&(string_table[idx_json_key_water0])));
					    strcat(json, string_buffer);
					    dtostrf(water0Temp, 4, 2, float_buffer);
					    strcat(json, float_buffer);

					    strcpy_P(string_buffer, (char*)pgm_read_word(&(string_table[idx_json_key_water1])));
					    strcat(json, string_buffer);
					    dtostrf(water1Temp, 4, 2, float_buffer);
					    strcat(json, float_buffer);

					    strcpy_P(string_buffer, (char*)pgm_read_word(&(string_table[idx_json_key_co2])));
					    strcat(json, string_buffer);
					    dtostrf(CO2PPM, 4, 2, float_buffer);
					    strcat(json, float_buffer);

					    strcpy_P(string_buffer, (char*)pgm_read_word(&(string_table[idx_json_key_leak0])));
					    strcat(json, string_buffer);
					    itoa(waterLevel0, float_buffer, 10);
					    strcat(json, float_buffer);

					    strcpy_P(string_buffer, (char*)pgm_read_word(&(string_table[idx_json_key_leak1])));
					    strcat(json, string_buffer);
					    itoa(waterLevel1, float_buffer, 10);
					    strcat(json, float_buffer);

					    strcpy_P(string_buffer, (char*)pgm_read_word(&(string_table[idx_json_key_photo])));
					  	strcat(json, string_buffer);
					  	itoa(photo, float_buffer, 10);
					  	strcat(json, float_buffer);

					  strcat(json, json_bracket_close);

					  strcpy_P(string_buffer, (char*)pgm_read_word(&(string_table[idx_json_key_channels])));
					  strcat(json, string_buffer);
					  for(int i=0; i<CHANNEL_SIZE; i++) {
						itoa(channels[i], sPin, 10);
						itoa(digitalRead(channels[i]), state, 10);

						strcat(json, state);
						if(i + 1 < CHANNEL_SIZE) {
						  strcat(json, ",");
						}
					  }
					  strcat(json, json_array_bracket_close);

					strcat(json, json_bracket_close);
				}

				// /timer/{channel}/{seconds}
				else if (strncmp(resource, "timer", 5) == 0) {

					if(param1 == NULL || param1 == "") {
						#if DEBUG
							Serial.println("parameter required");
						#endif
						//send500("parameter required");
						break;
					}

					int channel = atoi(param1);
					unsigned long duration = strtoul(param2, NULL, 10);

					if(channel >= 0 && channel < CHANNEL_SIZE && duration > 0) {

						#if DEBUG
						  Serial.print("Channel: ");
						  Serial.println(channel);

						  Serial.print("Duration: ");
						  Serial.println(duration);
						#endif

						channel_table[channel][0] = channels[channel];
						channel_table[channel][1] = millis();
						channel_table[channel][2] = duration * 1000;

						digitalWrite(channels[channel], HIGH);
					}
					else {
					  #if DEBUG
						Serial.println("Invalid channel/duration");
					  #endif
					}

					strcpy(json, json_bracket_open);

						strcat(json, "\"channel\":");
						itoa(channel, float_buffer, 10);
						strcat(json, float_buffer);

						strcat(json, ",\"duration\":");
						itoa(duration, float_buffer, 10);
						strcat(json, float_buffer);

					strcat(json, json_bracket_close);
				}

				// /switch/?     1 = on, else off
				else if (strncmp(resource, "switch", 6) == 0) {

					bool valid = false;
					int channel = atoi(param1);
					int position = atoi(param2);

					if(channel >= 0 && channel < CHANNEL_SIZE) {
						valid = true;
					}

					if(valid) {

						position == 1 ? switchOn(channels[channel]) : switchOff(channels[channel]);

						strcpy(json, json_bracket_open);

						  strcpy_P(string_buffer, (char*)pgm_read_word(&(string_table[idx_json_key_channel])));
						  strcat(json, string_buffer);
						  strcat(json, param1);

						  strcpy_P(string_buffer, (char*)pgm_read_word(&(string_table[idx_json_key_pin])));
						  strcat(json, string_buffer);
						  itoa(channels[channel], string_buffer, 10);
						  strcat(json, string_buffer);

						  strcpy_P(string_buffer, (char*)pgm_read_word(&(string_table[idx_json_key_position])));
						  strcat(json, string_buffer);
						  itoa(digitalRead(channels[channel]), string_buffer, 10);
						  strcat(json, string_buffer);

						strcat(json, json_bracket_close);

						#if DEBUG
							Serial.print("/switch: ");
							Serial.println(json);
						#endif
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

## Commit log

2019-02-10 add co2 and water level sensors
2019-02-27 shorten rest variable names
    [main.cpp]
2019-03-06 add photo sensor and dehu pin
2019-03-10 move strings to progmem. add dehu and fan endpoints. only enable/print to serial if DEBUG enabled
2019-03-10 optimize memory. expose remaining analog and digital pins as switches
2019-03-10 revert to default mac address
    [main.cpp]
2019-03-13 fix memory leak. add eeprom library
    [main.cpp]
2019-03-27 eeprom mac/ip. add /reset endpoint
    [main.cpp]
2019-04-03 fix json formatting bug
    [main.cpp]
2019-04-05 output json channel ids instead of pin numbers
2019-04-05 fix invalid channel when channel is 0 bug
    [main.cpp]
2019-05-08 add 2nd and 3rd DHT sensors. refactor switch endpoint to return channel and pin
2019-06-12 fix example curl eeprom default ip. optimize switch resource
    [main.cpp]
2020-02-04 add kicad project
    [cropdroid-room-B_Cu.gbl, cropdroid-room-B_Mask.gbs, cropdroid-room-B_Paste.gbp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]
2020-02-05 finalize prototype v0.1a
    [cropdroid-room-B_Cu.gbl, cropdroid-room-B_Mask.gbs, cropdroid-room-B_Paste.gbp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]
2020-02-10 upgrade hardware to v0.2a (120v)
    [bom.csv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]
2020-02-10 final kicad v0.2a
    [bom.csv, cropdroid-room.kicad_pcb, cropdroid-room.sch]
2020-02-14 iterate on kicad room v0.3a
    [bom.csv, cropdroid-room.kicad_pcb, cropdroid-room.sch]
2020-02-14 fix kicad v0.3a co2 circuit missing diode and connection to microcontroller
    [cropdroid-room.kicad_pcb, cropdroid-room.sch]
2020-02-14 more v0.3a fixes
    [cropdroid-room.kicad_pcb, cropdroid-room.sch]
2020-02-14 add latest bom
    [bom.csv]
2020-02-21 room v0.4a
    [bom.csv, cropdroid-room.kicad_pcb, cropdroid-room.sch]
2020-03-02 add v0.5a hardware
    [bom.csv, cropdroid-room-B_Cu.dxf, cropdroid-room-B_Mask.dxf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]
2020-04-13 return metrics as array. refactor /timer, /reboot and /reset endpoints
    [main.cpp]
2021-07-27 fix memory leak and channel size bug. create test suite. change DHT pins 2 and 3 to A6 and A7
    [main.cpp]
2024-01-16 Add hardware flow image

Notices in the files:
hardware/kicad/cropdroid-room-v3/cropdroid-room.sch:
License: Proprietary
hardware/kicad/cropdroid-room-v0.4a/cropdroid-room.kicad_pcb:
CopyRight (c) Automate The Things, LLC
